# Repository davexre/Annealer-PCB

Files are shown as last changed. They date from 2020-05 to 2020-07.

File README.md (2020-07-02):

# Annealer PCB
 An Arduino shield for induction cartridge case annealers based on the GinaErick design. 

## Pictures!

- [Front of board design](images/AnnealerPCBv3-front.png)
- [Back of board design](images/AnnealerPCBv3-back.png)

Final boards will actually print with an inductor symbol on the front and back, too - OSH Park's rendering doesn't 
show it correctly. Pictures of the actual boards will replace the images here when they arrive.

## Origins
 This design began from a simple DIY induction based cartridge case annealer created by a couple people on the
 [accurateshooter.com forum](http://forum.accurateshooter.com/threads/induction-brass-annealer-redux.3908353/). 
 Get ready for some reading - as of this writing, that thread is over 103 pages long!
 
 After creating a working, basic, analog annealer, I decided it was time to convert the thing to digital 
 control, and started implementing Arduino based controls. That naturally led to implementing the Arduino
 shield here to make it easier and cleaner to hook up the Arduino to all of the necessary hardware.
 
 ## Features
 - Arduino Uno R3 format shield
 - Support for boards with 5v, 3.3v, and 2v ADCs
 - Sensors
   - Two thermistors
   - Voltage
   - Current
   - Two [break beam sensors](https://www.adafruit.com/product/2167)
 - Two buttons (typically, Start and Stop) via a 4-pin header
 - Two relays (typically, for Induction board and solenoid control)
 - Two auxiliary headers (signal pin and ground, could be used for a variety of control purposes)
 - Multipurpose header (3 signals and ground, can hook up an encoder with button, or any other use)
 - Two LEDs for troubleshooting and confirmation of code
 - I2C connector to add an LCD or other I2C based device
 - Power On LED connector for front panel
 - Reset button
 
 You can find a [Bill of Materials](BOM.md) in this repository, too.
 
 ## IMPORTANT NOTE
 
 If you use the I2C connector, be aware that you cannot use Proximity sensor 2 or Thermistor 2 on some boards (like
 the Arduino Uno). Any board that ties SDA and SCL pins to A4/A5 will encounter this issue. I recommend that you pick the
 functions you wish to use, and only install connectors or headers for those functions (ie, only install the I2C connector
 **or** the Proximity 2 and Thermistor 2 connectors!

 ## Example Implementation
 My code for implementation is here: https://github.com/davexre/Annealer-Control - note that I don't make use of 
 all of the features on this board at this time! 
 
 ## Configuration
 The board was originally designed with [SparkFun's](https://www.sparkfun.com/) [RedBoard Artemis](https://www.sparkfun.com/products/15444)
 in mind. The Artemis processor has ADCs that use 2v as their reference. They can safely handle 
 3.3v, but saturate at 2v. So, the board incorporates several voltage dividers to keep things within
 the scale that the ADCs can successfully read. The documentation here covers ways to configure the
 board for other reference voltages. There are four solderable open/closed jumper pads that you can
 use to alter several circuit paths appropriately. SparkFun has a [tutorial on using jumper pads](https://learn.sparkfun.com/tutorials/how-to-work-with-jumper-pads-and-pcb-traces) on their site.
 
 ### Pin Map
 ```
#ifdef _V4_BOARD
  #define  VOLTAGE_PIN     A0
  #define  CURRENT_PIN     A1
  #define  THERM1_PIN      A2
  #define  OPTO1_PIN       A3
  #define  THERM2_PIN      A4
  #define  OPTO2_PIN       A5
  #define  START_PIN       2   
  #define  STOP_PIN        3
  #define  INDUCTOR_PIN    4
  #define  SOLENOID_PIN    5
  #define  AUX1_PIN        6
  #define  AUX2_PIN        7   
  #define  INDUCTOR_LED    8
  #define  SOLENOID_LED    9
  #define  ENCODER_A_PIN   10
  #define  ENCODER_B_PIN   11
  #define  ENCODER_BUTTON  12
#endif
```

 ### Voltage
 Input to pin A0.
 
 The voltage sensor circuit expects to be fed by a voltage divider - I'm using an Octopus Voltage Divider Brick,
 which is a 16:1 voltage divider (see below). For a 48v power supply on the annealer, that means a maximum input voltage of 4v
 coming in to J1 on the board. The design then incoporates a second voltage divider using a 10k resistor and a 20k
 trimpot, so you can adjust the input voltage precisely to match the ADC (so, exactly 50% for the Artemis). 
 
 However, if you board supports 3.3v, you can set the trimpot to cut 4v down to 3.3v. For a 5v board, you can bypass the 
 on-board voltage divider completely by cutting the VOL-BYPASS jumper, and soldering the other side closed. This will
 pass the input on J1 directly to A0. Be careful! 
 
 It may also be possible to use the onboard voltage divider to cut the voltage back to anything reasonable. The design
 uses a [Bourns 3296W](https://www.bourns.com/pdfs/3296.pdf) trimpot, which is available in resistances up to 2Mohm.
 A 200kOhm trimpot could be used (instead of the spec'ed 20kOhm trimpot) in conjunction with the specified 10kOhm resistor
 to bring 48v in line with the ADC. But... I prefer to keep higher voltage off the shield, thus the voltage brick. 
 
 To tune the voltage divider after assembly, attach 5v to pin 1 at connector J1. Measure the voltage between A0 and GND.
 Tune trimpot VR1 until you measure 2.5v, indicating that the voltage divider network is dividing voltage by 2 exactly. 
 
 *Note:* it seems like the Octopus Voltage Divider Brick is no longer made by ElecFreaks. So, 
 I [ginned up another PCB design](https://github.com/davexre/Voltage-Divider-Brick) that implements something very
 similar to the Octopus brick. You can substitute whatever resistors you need to get the output voltage within the scale
 that your board can support. You could potentially just use the voltage divider already on the Annealer board to replace
 it, but personally, I prefer to keep potentially damaging voltages (pun intended) away from my main board. The brick 
 adds a small layer of protection, in this case.
 
 ### Current
 Input to pin A1.
 
 The current sensor circuit expects to receive the output from something like a Hall effect sensor, such as the [Gravity
 20A Current Sensor](https://www.dfrobot.com/product-1570.html) made by DF Robot. The pinout on J2 expects to power a 
 device, so pin 1 is 5V supply. Pin 2 is ground. Pin 3 is the return from the [ACS712 Hall effect sensor IC](http://www.allegromicro.com/~/media/Files/Datasheets/ACS712-Datasheet.ashx?la=en). The sensor returns 
 1/2 of the supply voltage at 0A (and can signal +/- 20A). At +20A, it returns 4.5v. 
 
 If you have a 5v board, you can safely bypass the voltage divider network by cutting the CUR-BYPASS jumper and soldering
 the other side closed. 
 
 For other boards, the voltage divider can be tuned to pull the max input value down to match the ADC reference voltage.
 Divide your reference voltage by 4.5 to get the scale factor, and then multiply by 5 to get a target voltage. For instance, 
 for the Artemis, 2/4.5 = .444. Multiply by 5v to get a target of 2.222 volts. For 3.3V reference, your target is 3.667.
 Attach 5v to pin 3 on J2, and then measure voltage between A1 and GND. Tune trimpot VR2 until you reach the target voltage. 
 
 For using sensors other than the Gravity sensor block lined above, you can use this circuit as needed. Changing the jumper
 setting links pin 3 on J2 to A1 directly, or you can simply use the voltage divider network to configure the correct input
 voltage for your sensor. 
 
 ### REF-VOLT jumper
 
 The REF-VOLT jumper feeds the thermistor and proximity sensors an appropriate logic level voltage for the board
 in use. To get accurate readings, and avoid damage to your board, you need to supply these devices with your reference
 voltage. 
 
 The default setting is 3.3v - you can easily cut the jumper and solder to the 5.5v side, as well.
 
 To configure for 5v, cut both the REF_VOLT jumper and resolder the opposite side. This connects the 5v
 supply to the thermistor voltage divider.

 ### Thermistors
 Input to pins A2 and A4, respectively. _**SEE NOTE ABOVE ABOUT I2C**_
 
 These are basic 10K nominal thermistors. They're generally used by wiring them in a voltage divider configuration with a
 10k resistor, and determining the resistance of the thermistor at the current temperature, and then cross referencing that
 to a table, or using a Steinhart style equation to arrive at the actual temperature. One example of [this kind of thermistor](https://www.adafruit.com/product/372_)
 is sold by Adafruit. 
 
 There's also a voltage divider feeding the thermistors to ensure they get the correct logic level voltage. That's easy if
 you have a 3.3v or 5v board. If you have an Artemis based board, though, you need to supply a  2v reference for accurate
 readings. So, we do that with a voltage divider on the board. By default, the board divides 3.3v (from the REF-VOLT jumper)
 down to 2v for the source voltage.
 
 To set this up, feed 3.3v into the 3.3v pin on the shield. Then probe the middle pad of the THERM_DIV jumper and GND.
 Adjust VR3 until you reach 2v.
 
 See "REF-VOLT jumper" above to determine how to send the correct source voltage to the thermistors. If you need to bypass 
 the voltage divider (to send 3.3v or 5v directly to the thermistors), cut the THERM-DIV jumper and solder to the other
 side. 

 ### Proximity Sensors
 Input to pins A3 and A5, respectively. _**SEE NOTE ABOVE ABOUT I2C**_
 
 J3 and J10 are both 5 pin jumpers that are intended to drive the [Adafruit IR Break Beam sensors](https://www.adafruit.com/product/2167). 
 
 Pin 1 connects to a digital pin, so you'll need to use A3 and A5 with digitalRead. You need to set INPUT_PULLUP on 
 those pins, as well. Pin 2 should be your reference voltage (3.3v or 5v) and is set by the REF-VOLT jumper (see above). 
 Pin 4 is 5v for the IR transmitter. Pins 3 and 5 are ground.

 ### Start/Stop buttons, relays, AUX, and Encoder connectors
 
 Each of these connectors provides direct access to one or more digital pins. You can use these for input or output as
 required. The example implementation uses the start/stop buttons, and the relays, currently. 
 
 J8 is a 4 pin connector with pins 2 & 4 connected to GND. Pin 1 connects to D6, and Pin 3 connects to D7. The intention
 here is to connect each pair to a basic momentary switch/button and use them for control over the anneal cycle. You likely
 want to use the INPUT_PULLUP option on the pin configuration, or implement your own pullup or pulldown resistor for each
 pin. 
 
 J6, J7, J9, and J11 are all two pin connectors. Pin 2 on each connects to GND. Pin 1 connects as follows: J6 - D4, J7 - D5,
 J9 - D2, J11 - D3. The example uses J6 and J7 to operate the inductor board SSR, and the trapdoor solenoid SSR, 
 respectively.
 
 The Encoder connector provides access to 3 additional digital pins (D10 on pin 1, D11 on pin 2, D12 on pin3), with
 the fourth pin connecting to GND. This could be used for any purpose required, but one common purpose might be to interface
 with an encoder knob and click switch. 

 ### I2C
 
 _**SEE NOTE ABOVE ABOUT PIN CONFLICTS WITH I2C AND OTHER DEVICES**_
 
 The I2C connector breaks out GND on pin 1, VCC (selectable 3.3V or 5V) on pin 2, SDA on pin 3, and SCL on pin 4, similar
 to the pin order found on common I2C LCDs. This gives you a way to connect any I2C device to your board. Between this and
 the Multipurpose connector, you can easily implement an LCD and clickable encoder for input and display. 
 
 There's a solderable jumper for voltage selection. It defaults to 3.3v, with 5V selectable on the other side of the jumper.
 Obviously, use the correct voltage for your device(s)!

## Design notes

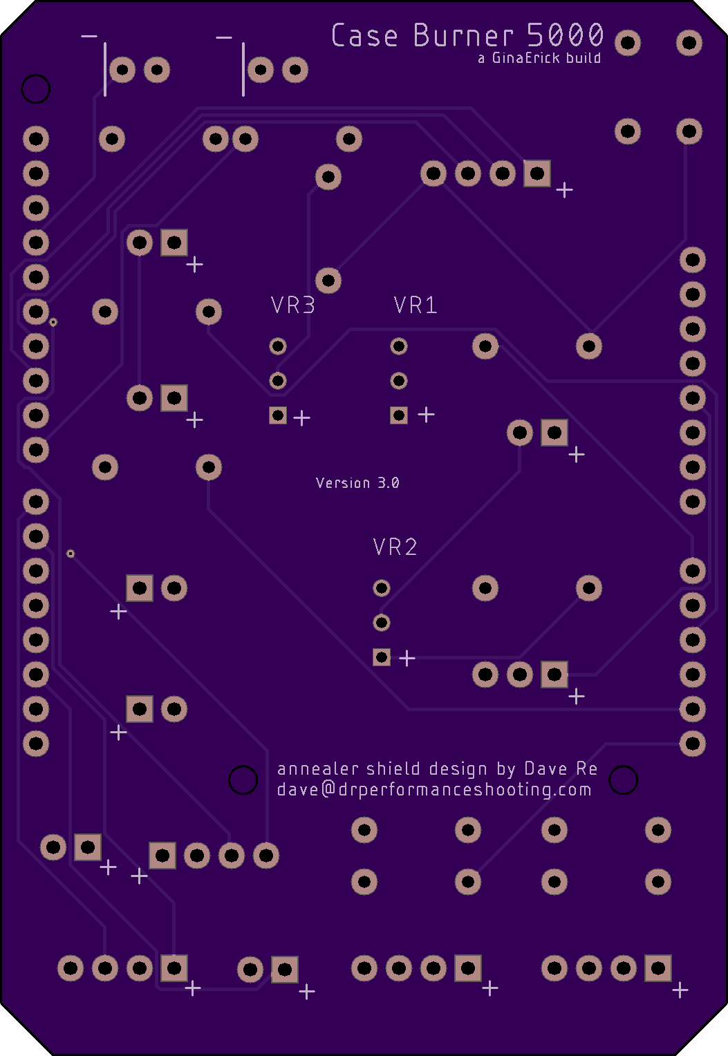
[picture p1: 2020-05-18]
images/AnnealerPCBv3-back.png

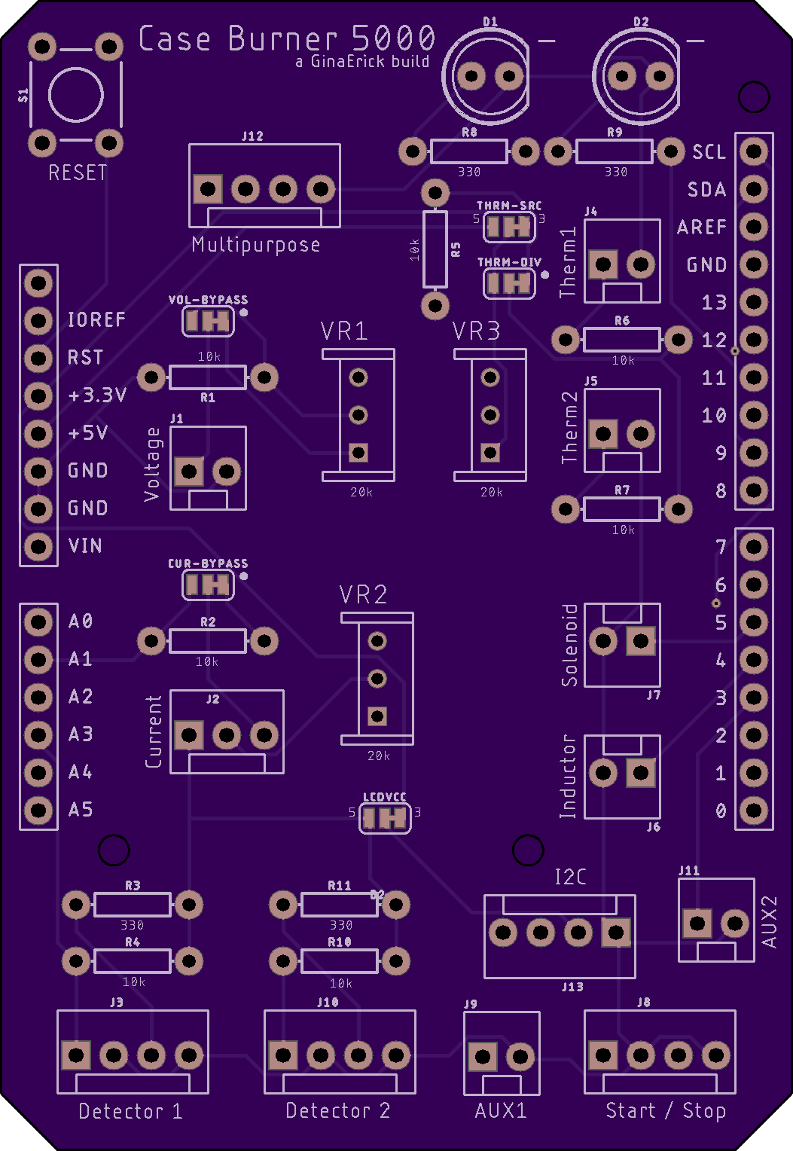
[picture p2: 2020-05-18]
images/AnnealerPCBv3-front.png

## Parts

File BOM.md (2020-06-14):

# Annealer PCB BOM

In addition to the Annealer shield board, you'll need some components to finish out the build and use the shield.
This Bill of Materials lists out the set of parts required to assemble the whole thing, and suggested purchase
locations for each. 

## Parts List

- 2x 5mm LEDs
- Molex Polarized Connectors
  - 8x 1x2
  - 1x 1x3
  - 3x 1x4
  - 2x 1x5
- 3x Bourns 3296W-1-203ALF trimpots
- 5x 10k ohm axial lead resistor
- 3x 330 ohm axial lead resistor
- 1x mini pushbutton SPST switch
- stackable headers or male headers

### Connectors

Molex makes a number of different versions. The board is designed for .1" (2.54mm) pitch connectors, but you can even use
male headers, if that's your preference. Some examples from SparkFun:

- https://www.sparkfun.com/products/8233
- https://www.sparkfun.com/products/8232
- https://www.sparkfun.com/products/8231

And the corresponding connectors for your cables (don't forget the pins!):

- https://www.sparkfun.com/products/8095
- https://www.sparkfun.com/products/8096
- https://www.sparkfun.com/products/8097
- https://www.sparkfun.com/products/8100

A number of examples are available from Mouser and other places, too. For instance:

- https://www.mouser.com/ProductDetail/molex/22-23-2021/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
- https://www.mouser.com/ProductDetail/molex/22-11-2036/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
- https://www.mouser.com/ProductDetail/molex/22-23-2042/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
- https://www.mouser.com/ProductDetail/Molex/22-23-2051?qs=ILqg114nvd59B%2FNFe4wunQ%3D%3D

And the corresponding connectors and pins:

- https://www.mouser.com/ProductDetail/molex/10-11-2023/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
- https://www.mouser.com/ProductDetail/molex/10-11-2033/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
- https://www.mouser.com/ProductDetail/molex/10-11-2043/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
https://www.mouser.com/ProductDetail/molex/10-11-2053/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
- https://www.mouser.com/ProductDetail/molex/50-29-1900-cut-strip/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

### Trimpots

Really, any trimpot 10k or higher will work, as long as it has .1" pitch with three inline pins. The Bourns 3296W is what 
the board was designed for. 

https://www.mouser.com/Passive-Components/Potentiometers-Trimmers-Rheostats/Trimmer-Resistors-Through-Hole/_/N-9q0yt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

Alternately, you could choose to avoid the trimpot, and just solder in axial resistors between pins 1 & 2 on the board
footprint. To get best results, you'd want precision resistors, which may or may not end up cheaper than the trimpot,
depending on what you choose...

### Switch

This is just the usual PTH momentary switch that gets used in Arduino projects.

https://www.sparkfun.com/products/97

### LEDs and resistors

Take your pick - these are the normal fare. The resistors are all normal axial lead, 1/4 watt resistors. I used 1%, but since
you're trimming these, you can use 5% or even 10%, if you like. 

### Headers

Traditionally, you'd want stackable headers, so that you can also plug other devices into the top of your shield. SparkFun
has a ready-made set here: https://www.sparkfun.com/products/10007

However, if you want to rock straight male headers on the bottom, be my guest! https://www.sparkfun.com/products/116

You can find the same on Mouser, including that same SparkFun kit: https://www.mouser.com/ProductDetail/SparkFun/PRT-11417?qs=WyAARYrbSnb%252BtXjDIp5vcQ%3D%3D

The breakaway male headers come in many varieties.

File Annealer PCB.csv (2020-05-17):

Part | Value | Device | Package | Description | ADJUSTMENT_TYPE | CATEGORY | DESCRIPTION | DOCUMENTATION_LINK | DOCUMENTATION_URL | FAMILY | MANUFACTURER | MOUNTING_TYPE | NUMBER_OF_TURNS | PART_NUMBER | POWER | PROD_ID | RESISTANCE | RESISTIVE_MATERIAL | SERIES | SF_ID | SF_SKU | SIZE | STANDARD_PACKAGE | SUPPLIER_ITEM_LINK | SUPPLIER_ITEM_NUMBER | SUPPLIER_ITEM_URL | SUPPLIER_LINK | SUPPLIER_NAME | SUPPLIER_URL | TEMPERATURE_COEFFICIENT | TERMINATION_STYLE | TOLERANCE | VALUE
B2 | ARDUINO_UNO_R3_SHIELDUNO_R3_SHIELD_LABELS_HOLES_LONGER | ARDUINO_UNO_R3_SHIELDUNO_R3_SHIELD_LABELS_HOLES_LONGER | UNO_R3_SHIELD_HOLES_LONGER | Arduino R3 Shield Footprint
CUR-BYPASS | JUMPER-SMT_3_1-NC_TRACE_SILK | JUMPER-SMT_3_1-NC_TRACE_SILK | SMT-JUMPER_3_1-NC_TRACE_SILK | Normally closed trace jumper (1 of 2 connections)
D1 |  | LED5MM | LED_5MM | LED (Generic)
D2 |  | LED5MM | LED_5MM | LED (Generic)
J1 |  | CONN_02POLAR | MOLEX-1X2 | Multi connection point. Often used as Generic Header-pin footprint for 0.1 inch spaced/style header connections |  |  |  |  |  |  |  |  |  |  |  |  |  |  |  | PRT-09918
J2 |  | CONN_03POLAR | MOLEX-1X3 | Multi connection point. Often used as Generic Header-pin footprint for 0.1 inch spaced/style header connections |  |  |  |  |  |  |  |  |  |  |  | CONN-08625 |  |  |  | PRT-08096
J3 |  | CONN_04POLAR | MOLEX-1X4 | Multi connection point. Often used as Generic Header-pin footprint for 0.1 inch spaced/style header connections |  |  |  |  |  |  |  |  |  |  |  | CONN-08186 |  |  |  | PRT-08231
J4 |  | CONN_02POLAR | MOLEX-1X2 | Multi connection point. Often used as Generic Header-pin footprint for 0.1 inch spaced/style header connections |  |  |  |  |  |  |  |  |  |  |  |  |  |  |  | PRT-09918
J5 |  | CONN_02POLAR | MOLEX-1X2 | Multi connection point. Often used as Generic Header-pin footprint for 0.1 inch spaced/style header connections |  |  |  |  |  |  |  |  |  |  |  |  |  |  |  | PRT-09918
J6 |  | CONN_02POLAR | MOLEX-1X2 | Multi connection point. Often used as Generic Header-pin footprint for 0.1 inch spaced/style header connections |  |  |  |  |  |  |  |  |  |  |  |  |  |  |  | PRT-09918
J7 |  | CONN_02POLAR | MOLEX-1X2 | Multi connection point. Often used as Generic Header-pin footprint for 0.1 inch spaced/style header connections |  |  |  |  |  |  |  |  |  |  |  |  |  |  |  | PRT-09918
J8 |  | CONN_04POLAR | MOLEX-1X4 | Multi connection point. Often used as Generic Header-pin footprint for 0.1 inch spaced/style header connections |  |  |  |  |  |  |  |  |  |  |  | CONN-08186 |  |  |  | PRT-08231
J9 |  | CONN_02POLAR | MOLEX-1X2 | Multi connection point. Often used as Generic Header-pin footprint for 0.1 inch spaced/style header connections |  |  |  |  |  |  |  |  |  |  |  |  |  |  |  | PRT-09918
J10 |  | CONN_04POLAR | MOLEX-1X4 | Multi connection point. Often used as Generic Header-pin footprint for 0.1 inch spaced/style header connections |  |  |  |  |  |  |  |  |  |  |  | CONN-08186 |  |  |  | PRT-08231
J11 |  | CONN_02POLAR | MOLEX-1X2 | Multi connection point. Often used as Generic Header-pin footprint for 0.1 inch spaced/style header connections |  |  |  |  |  |  |  |  |  |  |  |  |  |  |  | PRT-09918
J12 |  | CONN_04POLAR | MOLEX-1X4 | Multi connection point. Often used as Generic Header-pin footprint for 0.1 inch spaced/style header connections |  |  |  |  |  |  |  |  |  |  |  | CONN-08186 |  |  |  | PRT-08231
J13 |  | CONN_04POLAR | MOLEX-1X4 | Multi connection point. Often used as Generic Header-pin footprint for 0.1 inch spaced/style header connections |  |  |  |  |  |  |  |  |  |  |  | CONN-08186 |  |  |  | PRT-08231
LCDVCC | JUMPER-SMT_3_1-NC_TRACE_SILK | JUMPER-SMT_3_1-NC_TRACE_SILK | SMT-JUMPER_3_1-NC_TRACE_SILK | Normally closed trace jumper (1 of 2 connections)
R1 | 10k | 10KOHM-HORIZ-1/4W-1% | AXIAL-0.3 | 10kΩ resistor |  |  |  |  |  |  |  |  |  |  |  | RES-12183 |  |  |  |  |  |  |  |  |  |  |  |  |  |  |  |  | 10k
R2 | 10k | 10KOHM-HORIZ-1/4W-1% | AXIAL-0.3 | 10kΩ resistor |  |  |  |  |  |  |  |  |  |  |  | RES-12183 |  |  |  |  |  |  |  |  |  |  |  |  |  |  |  |  | 10k
R3 | 330 | 330OHM-HORIZ-1/10W-5% | AXIAL-0.3 | 330Ω resistor |  |  |  |  |  |  |  |  |  |  |  | RES-8371 |  |  |  |  |  |  |  |  |  |  |  |  |  |  |  |  | 330
R4 | 10k | 10KOHM-HORIZ-1/4W-1% | AXIAL-0.3 | 10kΩ resistor |  |  |  |  |  |  |  |  |  |  |  | RES-12183 |  |  |  |  |  |  |  |  |  |  |  |  |  |  |  |  | 10k
R5 | 10k | 10KOHM-HORIZ-1/4W-1% | AXIAL-0.3 | 10kΩ resistor |  |  |  |  |  |  |  |  |  |  |  | RES-12183 |  |  |  |  |  |  |  |  |  |  |  |  |  |  |  |  | 10k
R6 | 10k | 10KOHM-HORIZ-1/4W-1% | AXIAL-0.3 | 10kΩ resistor |  |  |  |  |  |  |  |  |  |  |  | RES-12183 |  |  |  |  |  |  |  |  |  |  |  |  |  |  |  |  | 10k
R7 | 10k | 10KOHM-HORIZ-1/4W-1% | AXIAL-0.3 | 10kΩ resistor |  |  |  |  |  |  |  |  |  |  |  | RES-12183 |  |  |  |  |  |  |  |  |  |  |  |  |  |  |  |  | 10k
R8 | 330 | 330OHM-HORIZ-1/10W-5% | AXIAL-0.3 | 330Ω resistor |  |  |  |  |  |  |  |  |  |  |  | RES-8371 |  |  |  |  |  |  |  |  |  |  |  |  |  |  |  |  | 330
R9 | 330 | 330OHM-HORIZ-1/10W-5% | AXIAL-0.3 | 330Ω resistor |  |  |  |  |  |  |  |  |  |  |  | RES-8371 |  |  |  |  |  |  |  |  |  |  |  |  |  |  |  |  | 330
R10 | 10k | 10KOHM-HORIZ-1/4W-1% | AXIAL-0.3 | 10kΩ resistor |  |  |  |  |  |  |  |  |  |  |  | RES-12183 |  |  |  |  |  |  |  |  |  |  |  |  |  |  |  |  | 10k
R11 | 330 | 330OHM-HORIZ-1/10W-5% | AXIAL-0.3 | 330Ω resistor |  |  |  |  |  |  |  |  |  |  |  | RES-8371 |  |  |  |  |  |  |  |  |  |  |  |  |  |  |  |  | 330
S1 | MOMENTARY-SWITCH-SPST-PTH-6.0MM | MOMENTARY-SWITCH-SPST-PTH-6.0MM | TACTILE_SWITCH_PTH_6.0MM | Momentary Switch (Pushbutton) - SPST |  |  |  |  |  |  |  |  |  |  |  | SWCH-08441 |  |  |  |  | COM-00097
THRM-DIV | JUMPER-SMT_3_1-NC_TRACE_SILK | JUMPER-SMT_3_1-NC_TRACE_SILK | SMT-JUMPER_3_1-NC_TRACE_SILK | Normally closed trace jumper (1 of 2 connections)
THRM-SRC | JUMPER-SMT_3_1-NC_TRACE_SILK | JUMPER-SMT_3_1-NC_TRACE_SILK | SMT-JUMPER_3_1-NC_TRACE_SILK | Normally closed trace jumper (1 of 2 connections)
VOL-BYPASS | JUMPER-SMT_3_1-NC_TRACE_SILK | JUMPER-SMT_3_1-NC_TRACE_SILK | SMT-JUMPER_3_1-NC_TRACE_SILK | Normally closed trace jumper (1 of 2 connections)
VR1 | 20K | 3296W-1-103LF | W | Trim Potentiometer (Pot) | Tope Adjustment | Potentiometers, Variable Resistors | TRIMMER 10K OHM 0.5W PC PIN | <a href=http://www.bourns.com/data/global/pdfs/3296.pdf">Datasheet</a>" | http://www.bourns.com/data/global/pdfs/3296.pdf | Trimmer Potentiometers | Bourns Inc | Through Hole | 25 | 3296W-1-103LF | 0.5W, 1/2W |  | 10k | Cermet | Trimpt 3296 - Sealed |  |  | Rectangular - 0.375 x 0.190" Face x 0.395" H (9.53mm x 4.83mm x 10.03mm)" | 50 | <a href=http://www.digikey.com/product-detail/en/3296W-1-103LF/3296W-103LF-ND/1088045">Details</a>" | 3296W-103LF-ND | http://www.digikey.com/product-detail/en/3296W-1-103LF/3296W-103LF-ND/1088045 | <a href=http://www.digikey.com">Home Page</a>" | Digi-Key | http://www.digikey.com | 100ppm/C | PC Pin | 10%
VR2 | 20k | 3296W-1-103LF | W | Trim Potentiometer (Pot) | Tope Adjustment | Potentiometers, Variable Resistors | TRIMMER 10K OHM 0.5W PC PIN | <a href=http://www.bourns.com/data/global/pdfs/3296.pdf">Datasheet</a>" | http://www.bourns.com/data/global/pdfs/3296.pdf | Trimmer Potentiometers | Bourns Inc | Through Hole | 25 | 3296W-1-103LF | 0.5W, 1/2W |  | 10k | Cermet | Trimpt 3296 - Sealed |  |  | Rectangular - 0.375 x 0.190" Face x 0.395" H (9.53mm x 4.83mm x 10.03mm)" | 50 | <a href=http://www.digikey.com/product-detail/en/3296W-1-103LF/3296W-103LF-ND/1088045">Details</a>" | 3296W-103LF-ND | http://www.digikey.com/product-detail/en/3296W-1-103LF/3296W-103LF-ND/1088045 | <a href=http://www.digikey.com">Home Page</a>" | Digi-Key | http://www.digikey.com | 100ppm/C | PC Pin | 10%
VR3 | 20k | 3296W-1-103LF | W | Trim Potentiometer (Pot) | Tope Adjustment | Potentiometers, Variable Resistors | TRIMMER 10K OHM 0.5W PC PIN | <a href=http://www.bourns.com/data/global/pdfs/3296.pdf">Datasheet</a>" | http://www.bourns.com/data/global/pdfs/3296.pdf | Trimmer Potentiometers | Bourns Inc | Through Hole | 25 | 3296W-1-103LF | 0.5W, 1/2W |  | 10k | Cermet | Trimpt 3296 - Sealed |  |  | Rectangular - 0.375 x 0.190" Face x 0.395" H (9.53mm x 4.83mm x 10.03mm)" | 50 | <a href=http://www.digikey.com/product-detail/en/3296W-1-103LF/3296W-103LF-ND/1088045">Details</a>" | 3296W-103LF-ND | http://www.digikey.com/product-detail/en/3296W-1-103LF/3296W-103LF-ND/1088045 | <a href=http://www.digikey.com">Home Page</a>" | Digi-Key | http://www.digikey.com | 100ppm/C | PC Pin | 10%

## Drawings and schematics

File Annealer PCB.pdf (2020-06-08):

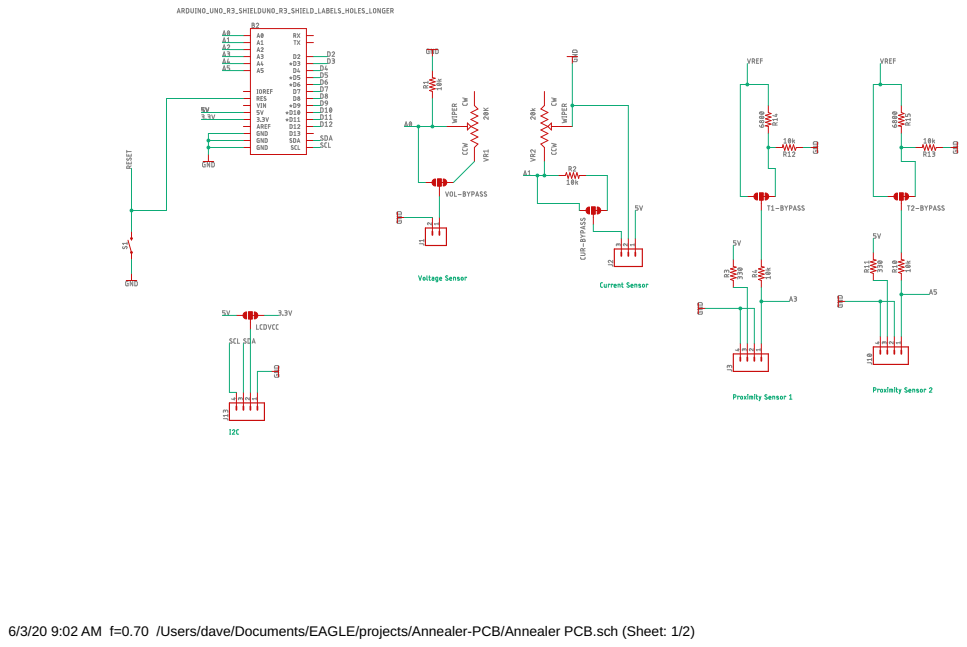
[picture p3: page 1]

6/3/20 9:02 AM f=0.70 /Users/dave/Documents/EAGLE/projects/Annealer-PCB/Annealer PCB.sch (Sheet: 1/2)

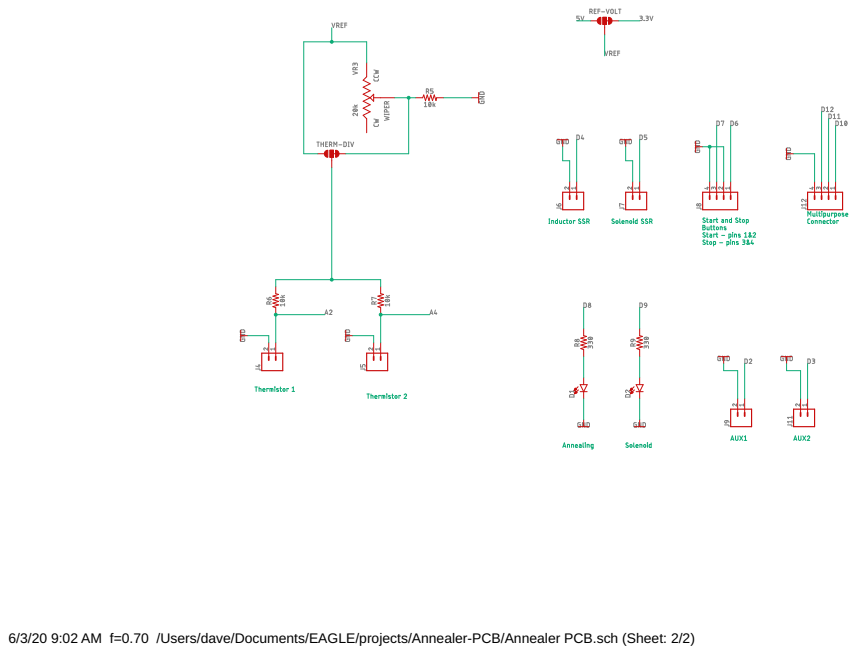
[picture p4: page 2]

6/3/20 9:02 AM f=0.70 /Users/dave/Documents/EAGLE/projects/Annealer-PCB/Annealer PCB.sch (Sheet: 2/2)

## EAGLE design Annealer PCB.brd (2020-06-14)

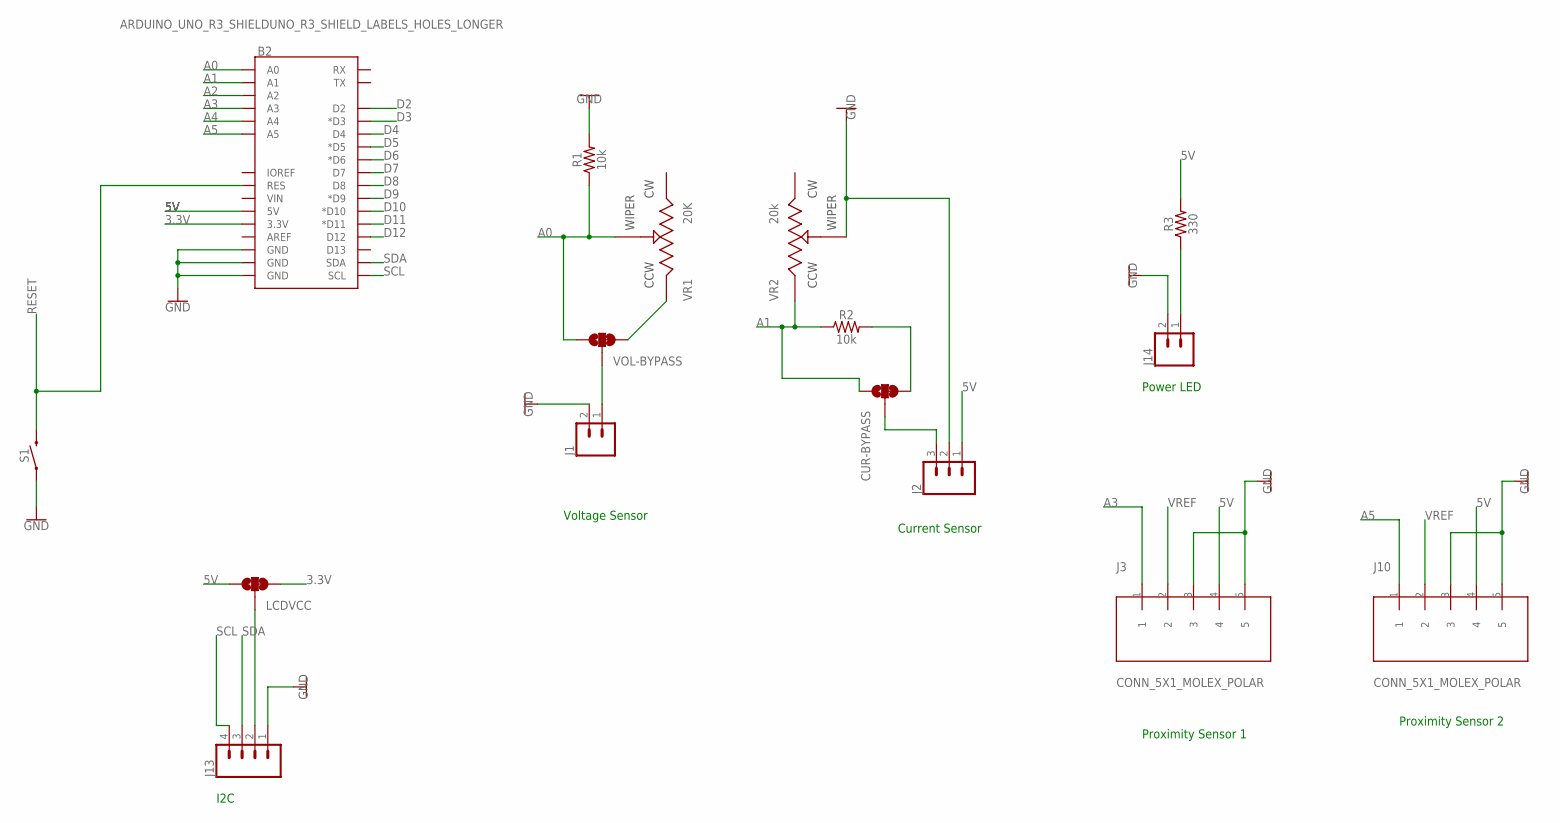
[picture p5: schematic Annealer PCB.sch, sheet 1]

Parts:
B2: ARDUINO_UNO_R3_SHIELDUNO_R3_SHIELD_LABELS_HOLES_L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; UNO_R3_SHIELD_HOLES_LONGER
CUR-BYPASS: JUMPER-SMT_3_1-NC_TRACE_SILK; SMT-JUMPER_3_1-NC_TRACE_SILK
J1, J14: CONN_02POLAR; MOLEX-1X2
J2: CONN_03POLAR; MOLEX-1X3
J3, J10: CONN_5X1_MOLEX_POLAR; MOLEX-5
J13: CONN_04POLAR; MOLEX-1X4
LCDVCC: JUMPER-SMT_3_1-NC_TRACE_SILK; SMT-JUMPER_3_1-NC_TRACE_SILK
R1, R2: 10k; AXIAL-0.3
R3: 330; AXIAL-0.3
S1: MOMENTARY-SWITCH-SPST-PTH-6.0MM; TACTILE_SWITCH_PTH_6.0MM
VOL-BYPASS: JUMPER-SMT_3_1-NC_TRACE_SILK; SMT-JUMPER_3_1-NC_TRACE_SILK
VR1: 20K; W
VR2: 20k; W

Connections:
3.3V: B2.3.3V, LCDVCC.3; also elsewhere on the board
5V: B2.5V, J2.1, J3.4, J10.4, LCDVCC.1, R3.P$2 (2); also elsewhere on the board
A0: B2.A0, R1.P$1 (1), VOL-BYPASS.1, VR1.2
A1: B2.A1, CUR-BYPASS.1, R2.P$1 (1), VR2.1
A2: B2.A2; also elsewhere on the board
A3: B2.A3, J3.1
A4: B2.A4; also elsewhere on the board
A5: B2.A5, J10.1
D2: B2.D2; also elsewhere on the board
D3: B2.D3 (*D3); also elsewhere on the board
D4: B2.D4; also elsewhere on the board
D5: B2.D5 (*D5); also elsewhere on the board
D6: B2.D6 (*D6); also elsewhere on the board
D7: B2.D7; also elsewhere on the board
D8: B2.D8; also elsewhere on the board
D9: B2.D9 (*D9); also elsewhere on the board
D10: B2.D10 (*D10); also elsewhere on the board
D11: B2.D11 (*D11); also elsewhere on the board
D12: B2.D12; also elsewhere on the board
GND: B2.GND@0 (GND), B2.GND@1 (GND), B2.GND@2 (GND), J1.2, J2.2, J3.3, J3.5, J10.3, J10.5, J13.1, J14.2, R1.P$2 (2), S1.1, VR2.2; also elsewhere on the board
unnamed: J14.1, R3.P$1 (1)
unnamed: CUR-BYPASS.2, J2.3
unnamed: CUR-BYPASS.3, R2.P$2 (2)
unnamed: VOL-BYPASS.3, VR1.1
unnamed: J1.1, VOL-BYPASS.2
unnamed: J13.2, LCDVCC.2
RESET: B2.RES, S1.3 (2)
SCL: B2.SCL, J13.4
SDA: B2.SDA, J13.3
VREF: J3.2, J10.2; also elsewhere on the board

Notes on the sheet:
Current Sensor
Voltage Sensor
Proximity Sensor 1
Proximity Sensor 2
I2C
Power LED

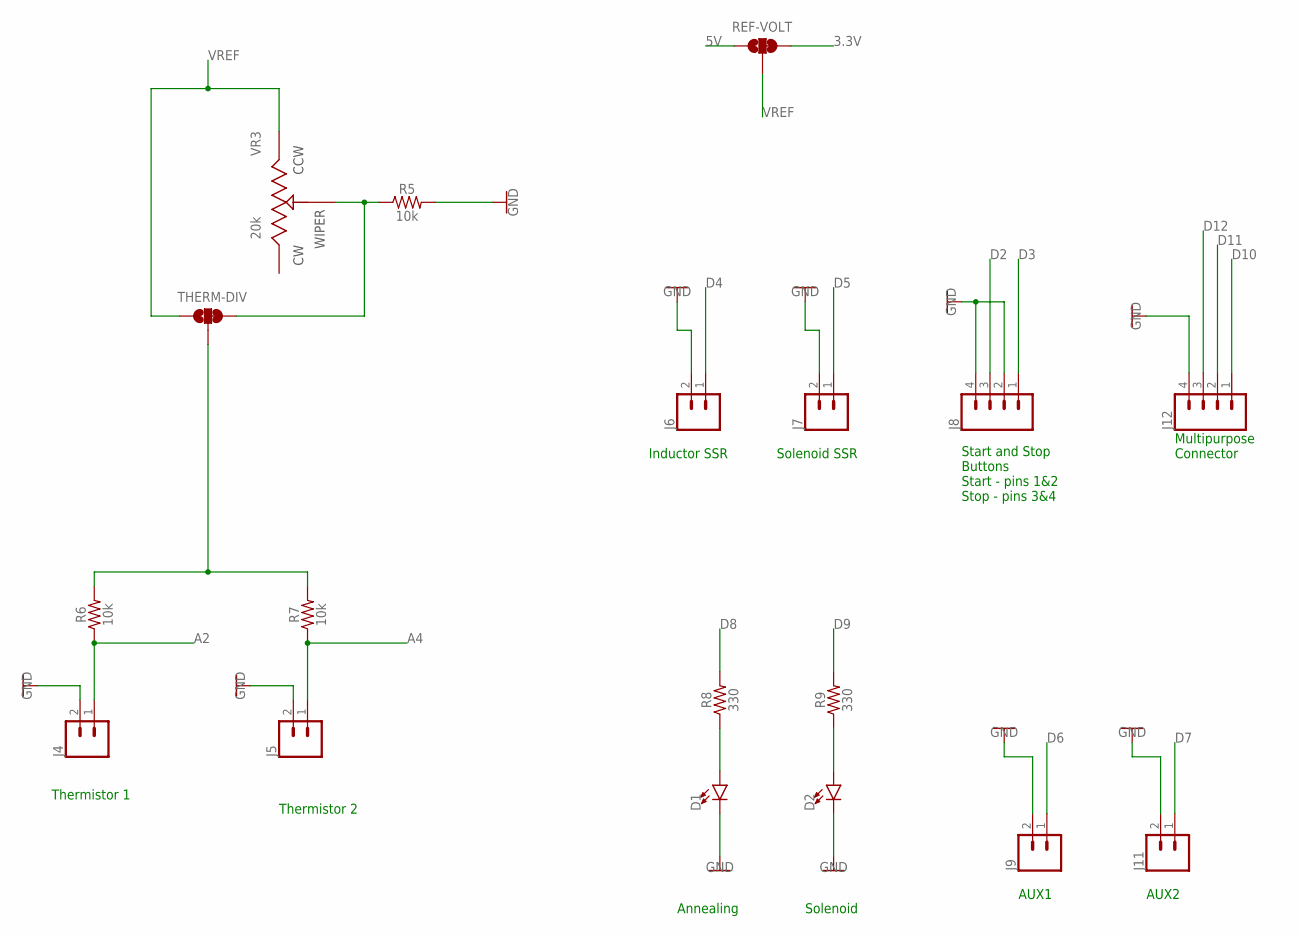
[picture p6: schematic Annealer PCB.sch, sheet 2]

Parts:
D1, D2: LED5MM; LED_5MM
J4, J5, J6, J7, J9, J11: CONN_02POLAR; MOLEX-1X2
J8, J12: CONN_04POLAR; MOLEX-1X4
R5, R6, R7: 10k; AXIAL-0.3
R8, R9: 330; AXIAL-0.3
REF-VOLT: JUMPER-SMT_3_1-NC_TRACE_SILK; SMT-JUMPER_3_1-NC_TRACE_SILK
THERM-DIV: JUMPER-SMT_3_1-NC_TRACE_SILK; SMT-JUMPER_3_1-NC_TRACE_SILK
VR3: 20k; W

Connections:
3.3V: REF-VOLT.3; also elsewhere on the board
5V: REF-VOLT.1; also elsewhere on the board
A2: J4.1, R6.P$1 (1); also elsewhere on the board
A4: J5.1, R7.P$1 (1); also elsewhere on the board
D2: J8.3; also elsewhere on the board
D3: J8.1; also elsewhere on the board
D4: J6.1; also elsewhere on the board
D5: J7.1; also elsewhere on the board
D6: J9.1; also elsewhere on the board
D7: J11.1; also elsewhere on the board
D8: R8.P$2 (2); also elsewhere on the board
D9: R9.P$2 (2); also elsewhere on the board
D10: J12.1; also elsewhere on the board
D11: J12.2; also elsewhere on the board
D12: J12.3; also elsewhere on the board
GND: D1.K (C), D2.K (C), J4.2, J5.2, J6.2, J7.2, J8.2, J8.4, J9.2, J11.2, J12.4, R5.P$2 (2); also elsewhere on the board
unnamed: D1.A, R8.P$1 (1)
unnamed: D2.A, R9.P$1 (1)
unnamed: R5.P$1 (1), THERM-DIV.3, VR3.2
SRC: R6.P$2 (2), R7.P$2 (2), THERM-DIV.2
VREF: REF-VOLT.2, THERM-DIV.1, VR3.1; also elsewhere on the board

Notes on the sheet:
Thermistor 1
Thermistor 2
Inductor SSR
Solenoid SSR
Annealing
Solenoid
Start and Stop Buttons Start - pins 1&2 Stop - pins 3&4
AUX1
AUX2
Multipurpose Connector

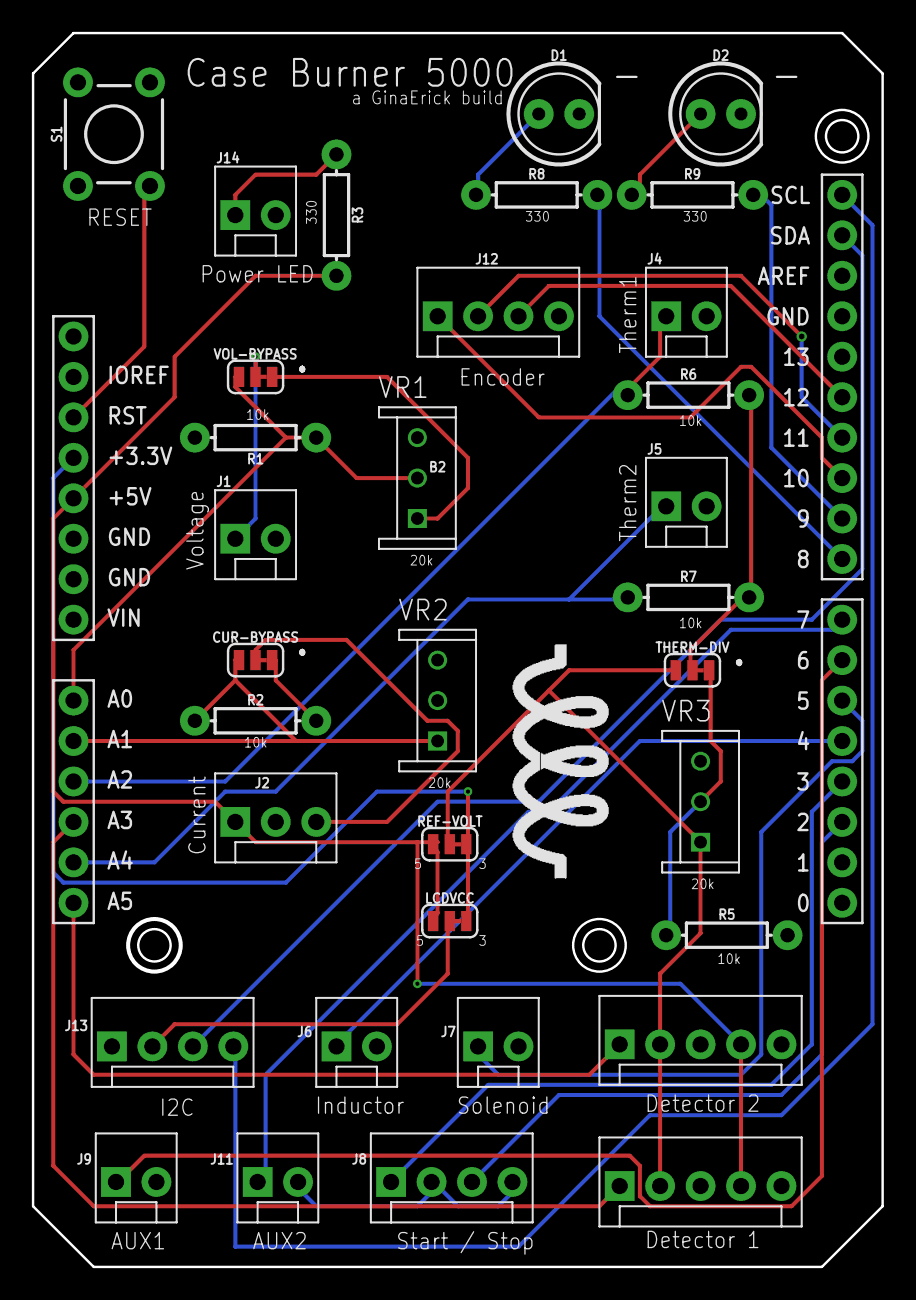
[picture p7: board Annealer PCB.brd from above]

Board: 2 copper layers, 53.3 x 77.5 mm, 34 parts (0 on the bottom side), 34 nets.

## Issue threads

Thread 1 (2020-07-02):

Change THERM_DIV to use diodes instead of a voltage divider!

davexre, 2020-07-02:
Using diodes should prevent changes in resistance on the whole circuit when we use multiple thermistors, and should prevent us from needing to tune a voltage divider.

davexre, 2020-07-02:
https://www.mouser.com/ProductDetail/Vishay-Semiconductors/RGP10B-E3-54?qs=lBalI7KQBwpCJMtDByN40g%3D%3D

This has 1.3V forward voltage - perfect for dropping 3.3 to 2.0.

davexre, 2020-07-10:
Resolved in V5.0

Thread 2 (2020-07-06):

Interference with power connector

davexre, 2020-07-06:
Top edge of board interferes with power connector on Artemis board, causing the PCB to be unable to seat. Need to notch that out, or move the shield connectors, or something.

davexre, 2020-07-10:
Resolved in v5.0

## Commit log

2020-05-15 Initial upload
    v3 of PCB design. Initial final.
    [Annealer PCB.brd, Annealer PCB.sch]
2020-05-16 Added I2C for an LCD or similar
    [Annealer PCB.brd, Annealer PCB.sch]
2020-05-16 Swap pins on thermistor2 and prox2
    [Annealer PCB.brd, Annealer PCB.sch]
2020-05-17 Inlcuding BOM CSV
    [Annealer PCB.csv, Annealer PCB.sch]
2020-05-17 Added additional silkscreen
    Added additional documentation on bottom silkscreen layer.
    [Annealer PCB.brd]
2020-05-18 Update Annealer PCB.brd
    [Annealer PCB.brd]
2020-05-18 Update on resistors vs. trimpot
2020-05-18 Add board images
2020-05-18 Add voltage divider brick design
2020-05-26 v3.1 - source voltage for phototransistors
    Source voltage was only 5v on v3.0. Changed design so that source voltage for thermistors AND phototransistors on the proximity sensors is fed by an appropriate reference voltage.
    [Annealer PCB.brd, Annealer PCB.sch]
2020-05-29 v3.2 - source voltage for proximity detectors
    Changed voltage handling for proximity sensors to avoid disrupting thermistor measurements when a phototransistor detects light inbound. Each phototransistor should have it's own input source and voltage divider. The thermistors share a common, separate input. Voltage dividers on each are bypassable.
    [Annealer PCB.brd, Annealer PCB.sch]
2020-05-30 v3.2 - minor trace movement
    [Annealer PCB.brd]
2020-05-31 Fixed hole sizes and moved things accordingly
    [Annealer PCB.brd]
2020-06-03 Added pin map
2020-06-04 Not a Stevie Ray Vaughn voltage divider
2020-06-08 Added PDF print of schematic
2020-06-12 Update for v4 board
2020-06-12 v4 board update
    [Annealer PCB.brd, Annealer PCB.sch]
2020-06-14 4.1 - add power-on LED
    [Annealer PCB.brd, Annealer PCB.sch]
2020-06-14 Add connector for power-on LED
2020-06-14 Add feature for Power On LED
2020-06-14 Label for Power ON LED
    [Annealer PCB.brd]

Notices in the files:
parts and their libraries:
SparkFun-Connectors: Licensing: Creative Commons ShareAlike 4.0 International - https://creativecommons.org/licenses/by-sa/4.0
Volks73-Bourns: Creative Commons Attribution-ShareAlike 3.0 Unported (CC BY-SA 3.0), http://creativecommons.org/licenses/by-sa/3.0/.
